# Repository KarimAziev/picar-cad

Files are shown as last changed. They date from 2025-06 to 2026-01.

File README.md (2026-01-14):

# About

This repository contains the 3D model source files for a four-wheeled robot chassis and steering system, written entirely in [OpenSCAD](https://openscad.org/). The design supports 3D printing and does not rely on external libraries.

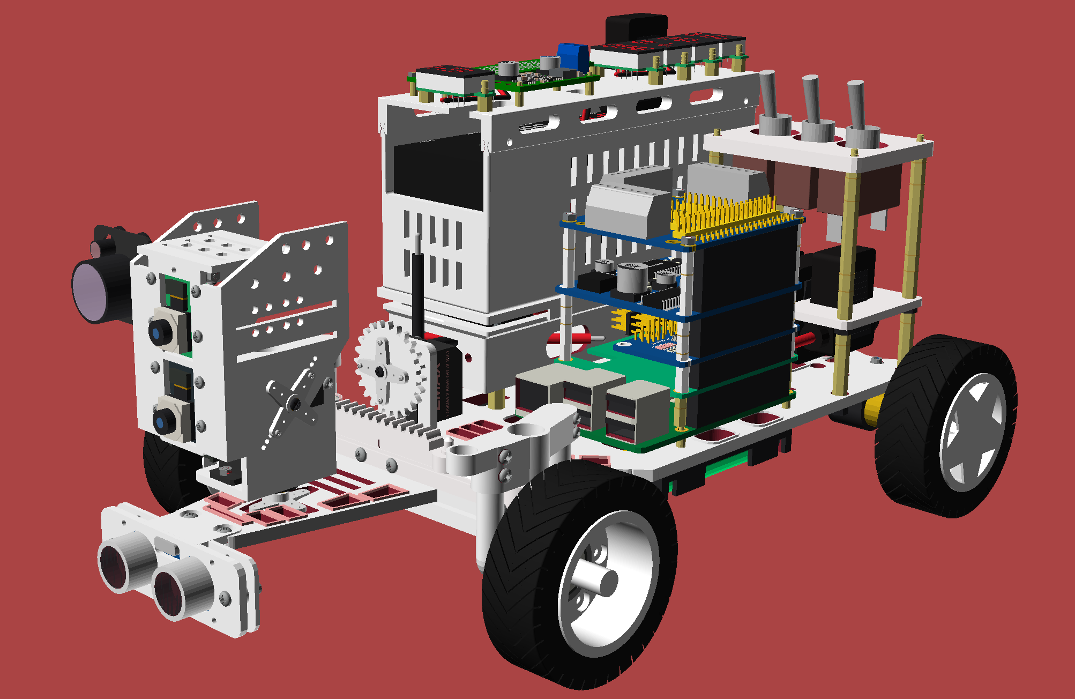
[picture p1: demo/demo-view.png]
Main View

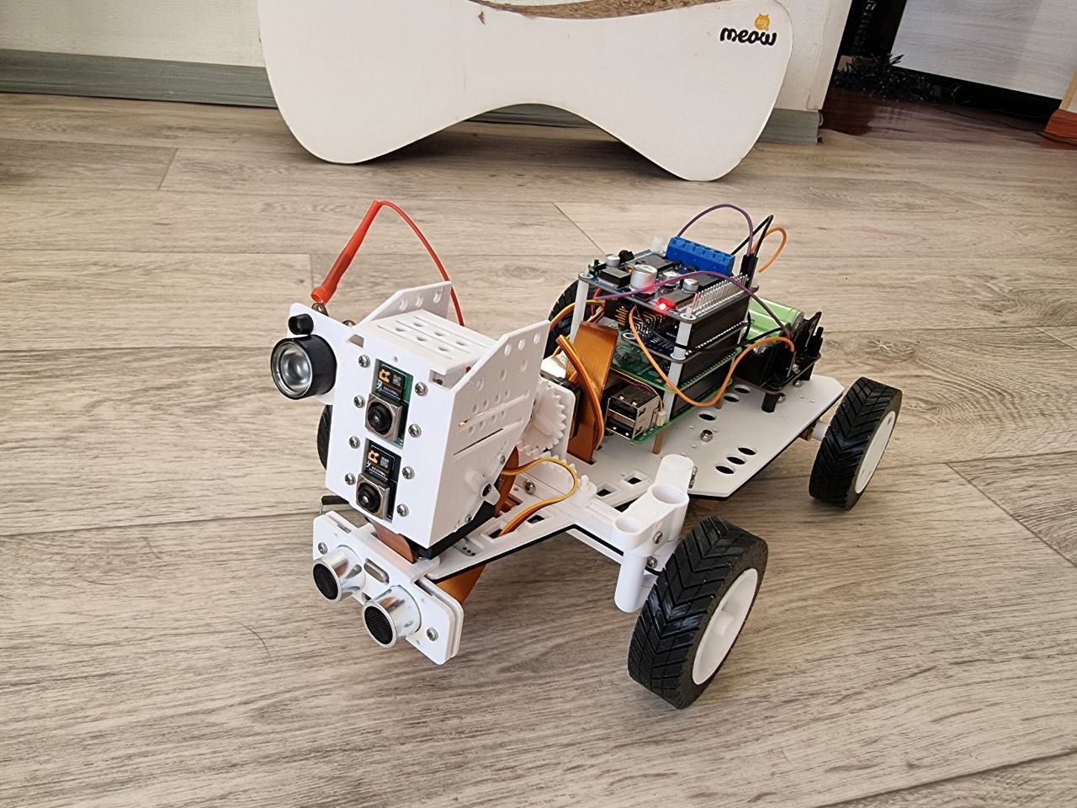
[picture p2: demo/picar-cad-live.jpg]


<!-- markdown-toc start - Don't edit this section. Run M-x markdown-toc-refresh-toc -->

**Table of Contents**

> - [About](#about)
>   - [Overview](#overview)
>     - [Requirements](#requirements)
>     - [CLI workflows (Makefile)](#cli-workflows-makefile)
>     - [Configurations](#configurations)
>     - [Validation (quick commands)](#validation-quick-commands)
>   - [Ackermann Geometry](#ackermann-geometry)
>   - [Assembly](#assembly)
>   - [Structure](#structure)
>   - [External Details](#external-details)
>     - [Bearings](#bearings)
>     - [Servos](#servos)
>     - [Raspberry Pi](#raspberry-pi)
>     - [Power Supply](#power-supply)
>       - [A Turnigy Rapid-style hardcase LiPo](#a-turnigy-rapid-style-hardcase-lipo)
>       - [UPS module S3](#ups-module-s3)
>       - [Preset swap checklist](#preset-swap-checklist)
>       - [Battery holders](#battery-holders)
>     - [Motors](#motors)
>     - [Camera Module](#camera-module)
>     - [Ultrasonic](#ultrasonic)
>     - [Switch buttons and fuses](#switch-buttons-and-fuses)
>     - [IR LED](#ir-led)
>     - [Bolts, Nuts and Standoffs](#bolts-nuts-and-standoffs)
>       - [Steering panel](#steering-panel)
>       - [Steering pinion](#steering-pinion)
>         - [For Servo gear](#for-servo-gear)
>         - [Self-tapping bolts for servo arm](#self-tapping-bolts-for-servo-arm)
>       - [Steering Knuckle](#steering-knuckle)
>       - [Raspberry Pi](#raspberry-pi-1)
>       - [Power case stack (default LiPo setup)](#power-case-stack-default-lipo-setup)
>         - [Shared bolts](#shared-bolts)
>         - [Socket case and lid](#socket-case-and-lid)
>         - [Power case and lid](#power-case-and-lid)
>       - [Battery holder](#battery-holder)
>       - [UPS module S3](#ups-module-s3-1)
>       - [Motor brackets](#motor-brackets)
>         - [For two N20 motors](#for-two-n20-motors)
>         - [For two standard (yellow) motors](#for-two-standard-yellow-motors)
>       - [Head](#head)
>         - [For two Raspberry Pi Camera Module 3 boards](#for-two-raspberry-pi-camera-module-3-boards)
>       - [Head neck](#head-neck)
>       - [IR Case for the Infrared LED Light Board](#ir-case-for-the-infrared-led-light-board)
>       - [Ultrasonic case for HC-SR04](#ultrasonic-case-for-hc-sr04)
>       - [Wheel hubs](#wheel-hubs)
>     - [Switch buttons and fuses](#switch-buttons-and-fuses-1)
>   - [Full BOM (default preset)](#full-bom-default-preset)
>   - [Full BOM (with UPS module S3)](#full-bom-with-ups-module-s3)

<!-- markdown-toc end -->

## Overview

The robot model is designed around the following core elements:

- **Ackermann Steering**: This design implements Ackermann steering and computes the steering radii from the robot parameters (not just by making the inner wheel turn more). The model calculates the trapezoid geometry automatically so you usually don’t need to tweak Ackermann-specific variables by hand.
- **Rear-Wheel Drive**: Two individual motors drive the rear wheels. Both standard yellow DC motors and N20-type motors are supported.
- **Modular Head Mount**: The head mount is designed to accommodate two Raspberry Pi Camera Module 3 or more sensors (e.g., day/night configuration).
- **Extendable Power Tiers**: Default power case for high-discharge LiPo packs (e.g., Turnigy Rapid 4S2P) plus battery holders plus slots for servo/motor driver HATs; Waveshare UPS S3 remains optional.
- **Raspberry Pi**: The chassis includes placements and bolt holes for the Raspberry Pi 5 and multiple 18650 battery holders.

### Requirements

Since `textmetrics` is used throughout the project, a nightly build of OpenSCAD is required. Also, be sure to enable `textmetrics` in the OpenSCAD editor via `Preferences -> Features -> textmetrics`. When using the CLI, pass `--enable=textmetrics` (e.g., `openscad --enable=textmetrics --backend=Manifold ...`).

### CLI workflows (Makefile)

- `make help` — list available targets.
- `make tests` — run all `tests/test_*.scad` suites; tolerates the empty top-level warning used by logic-only tests.
- `make assembly` — export `scad/assembly.scad` to `build/export/stl/assembly.stl` and `build/export/3mf/assembly.3mf` with `--backend=Manifold --enable=textmetrics --hardwarnings` and 3MF metadata.
- `make printable` — export `scad/printable.scad` and every file in `scad/printable_parts/` to flattened `build/export/stl/` and `build/export/3mf/` (tires prefer the TPU material hint; falls back if unsupported).
- `make all` — run tests, then build assembly and all printable exports.
- `make clean` — remove build outputs and test temp files.

### Configurations

Two main presets are supported: the default LiPo power case stack and the UPS S3 option. Both assume two battery holders. Jump to the BOMs for details: [Full BOM (default preset)](#full-bom-default-preset) or [Full BOM (with UPS module S3)](#full-bom-with-ups-module-s3).

### Validation (quick commands)

All commands require `--enable=textmetrics --backend=Manifold`.

```sh
# Full assembly preview (PNG)
openscad -o /tmp/scad-preview.png --preview --imgsize=754,934 --backend=Manifold --enable=textmetrics --camera=0,0,0,0,0,0,1100 scad/assembly.scad

# Utility tests
openscad --backend=Manifold --enable=textmetrics -o /tmp/test_functions.stl tests/test_functions.scad
openscad --backend=Manifold --enable=textmetrics -o /tmp/test_plist.stl tests/test_plist.scad
```

## Ackermann Geometry

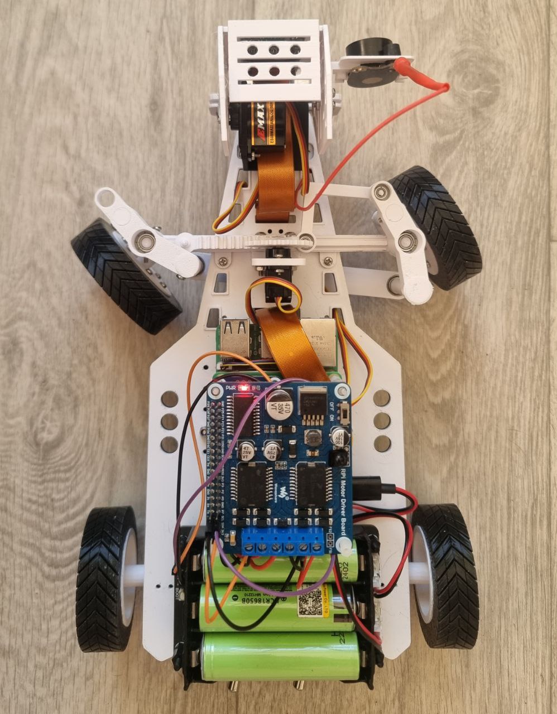
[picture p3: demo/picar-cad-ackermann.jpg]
Ackermann steering view


Ackermann steering is implemented with a rack-and-pinion mechanism that drives a single L-link (`rack_link`) mounted to one knuckle. That knuckle rotates when the rack moves, the opposite knuckle follows through a tie rod. The knuckles and tie rod form the Ackermann trapezoid, so the inside wheel turns more than the outside wheel.

> [!NOTE]
> Install the `rack_link` on only one side and on only one of the knuckles - it doesn't matter which. Movement of the rack will cause that "leading" knuckle to rotate. The leading knuckle is then connected to the second, "driven" knuckle via a tie rod.

Most parameters live in `scad/parameters.scad`, but the actual Ackermann geometry (angles and the required tie-rod top width) is calculated automatically from core robot dimensions such as chassis length, steering panel placement and knuckle geometry. Because of that, you will rarely need to edit Ackermann-specific variables manually - especially `steering_angle_deg`, which is derived from the layout.

## Assembly

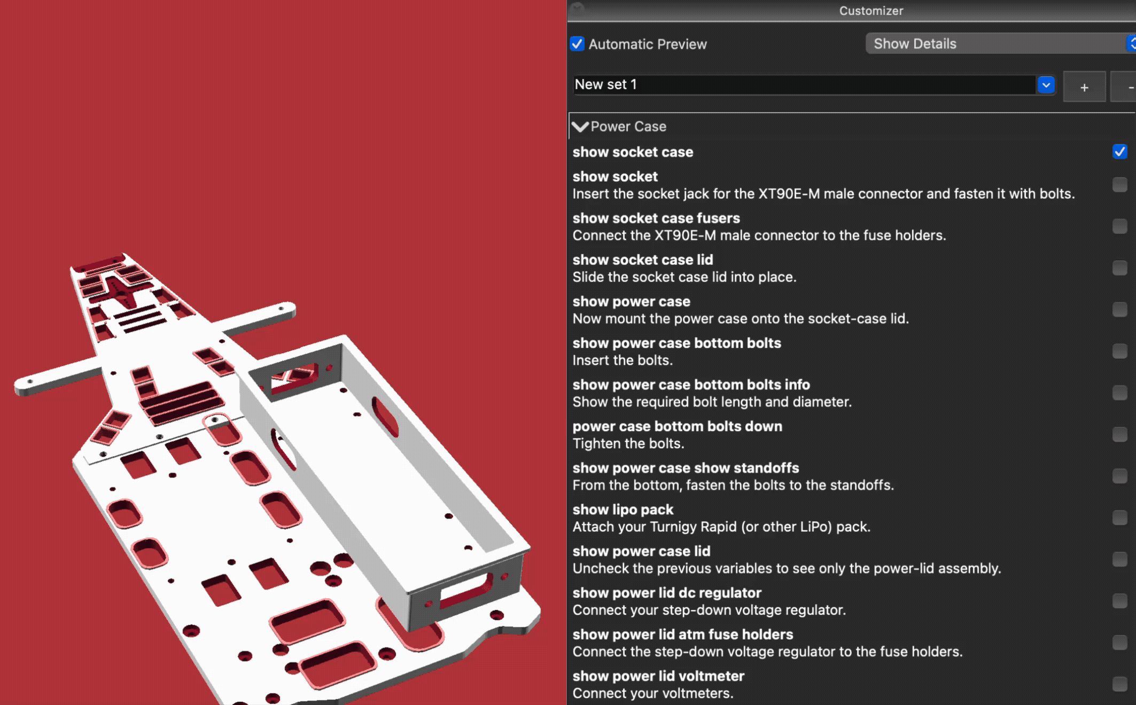
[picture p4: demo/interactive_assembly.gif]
Interactive Assembly


The interactive guide lives in `scad/assembly_guide.scad`. Open it in OpenSCAD and step through the boolean checkboxes in the built-in Customizer to reveal each assembly step (power case, steering, electronics, and wheels). For a static full build view, use `scad/assembly.scad`.

## Structure

The project is organized into several reusable modules under the scad/ directory:

- `parameters.scad`: Central configuration file containing physical dimensions (units are in millimeters).
- `power_lid_parameters.scad`: Configuration for the power case lid.
- `printable.scad`: Contains all printable parts in one place. You can print all parts except the tires using either PETG (recommended) or PLA. For the tires, use TPU (e.g., TPU 95A).
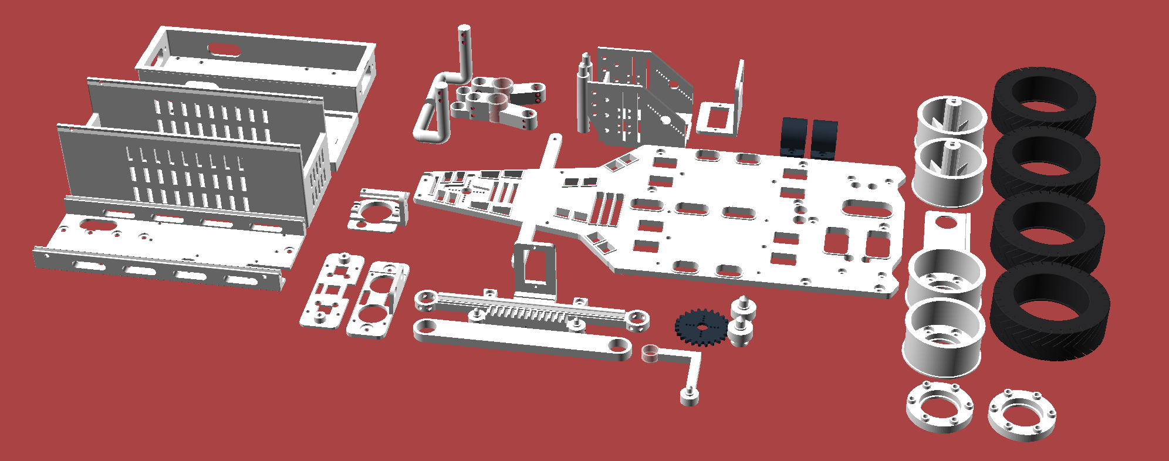
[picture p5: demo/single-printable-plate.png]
Single printable view
  
- `printable_parts/`: Individual printable part sources (one part per file) used by the Makefile for per-part exports.
- `assembly.scad`: Fully assembled view of the robot.
  Overview
- `assembly_guide.scad`: Interactive assembly. See [above](#assembly).
- `steering_system/`: Rack-and-pinion steering system based on Ackermann geometry.
- `power/`: Power case and related components.
- `components/chassis/`: Chassis and other components.
- `head/`: Mounting system for dual Raspberry Pi cameras.
- `motor_brackets/`: Brackets for both standard (yellow) and N20-style motors.
- `wheels/`: Components for rear and front wheels, including hubs and tires.
- `placeholders/`: Placeholder geometry for components such as the Raspberry Pi, servos, DC motors, battery holders, HATs, sensors, step-down voltage converters, INA260, etc. There’s a lot of stuff in there.
- `lib/`: Reusable modules. One important module is `lib/plist`, which provides helpers for working with property lists-a dict-like data structure used throughout the project because OpenSCAD doesn’t support dictionaries.

## External Details

All these details are just recommendations, you can use any other details, just don't forget to specify corresponding dimensions in `parameters.scad` and `power_lid_parameters.scad`. Reference renders and photos live in `demo/` (e.g., `demo/top-view.png`, `demo/ups_module_s3.png`, `demo/head_neck.png`, `demo/ultrasonic.png`).

### Bearings

- Four 685 (5x11x5) bearings: two are inserted into the steering knuckles and mounted on kingpin posts. To use different sizes, modify the variables `knuckle_bearing_outer_dia`, `knuckle_bearing_inner_dia`, and other relevant variables. The other two are inserted into the tie rod; the corresponding variables are `tie_rod_bearing_outer_dia`, `tie_rod_bearing_inner_dia`, and others.
- Two 693 (3x8x4) bearings are inserted into the rack link and into the knuckle arm that connects to the rack link. Both flanged and standard versions are supported.
- Two 608 (8x22x7) bearings are inserted into the front wheels.

### Servos

This project supports three **EMAX ES08MA II** servos by default. If using different models, update the following variables in `parameters.scad`:

- `steering_servo_slot_width` and `steering_servo_slot_height` for the steering servo
- `head_neck_pan_servo_slot_width` and `head_neck_pan_servo_slot_height` for the pan servo
- `head_neck_tilt_servo_slot_width` and `head_neck_tilt_servo_slot_height` for the tilt servo

### Raspberry Pi

Raspberry Pi 5 is supported by default. To use a different model, adjust the relevant variables prefixed with `rpi_` (e.g., `rpi_bolt_spacing`).

### Power Supply

#### A Turnigy Rapid-style hardcase LiPo

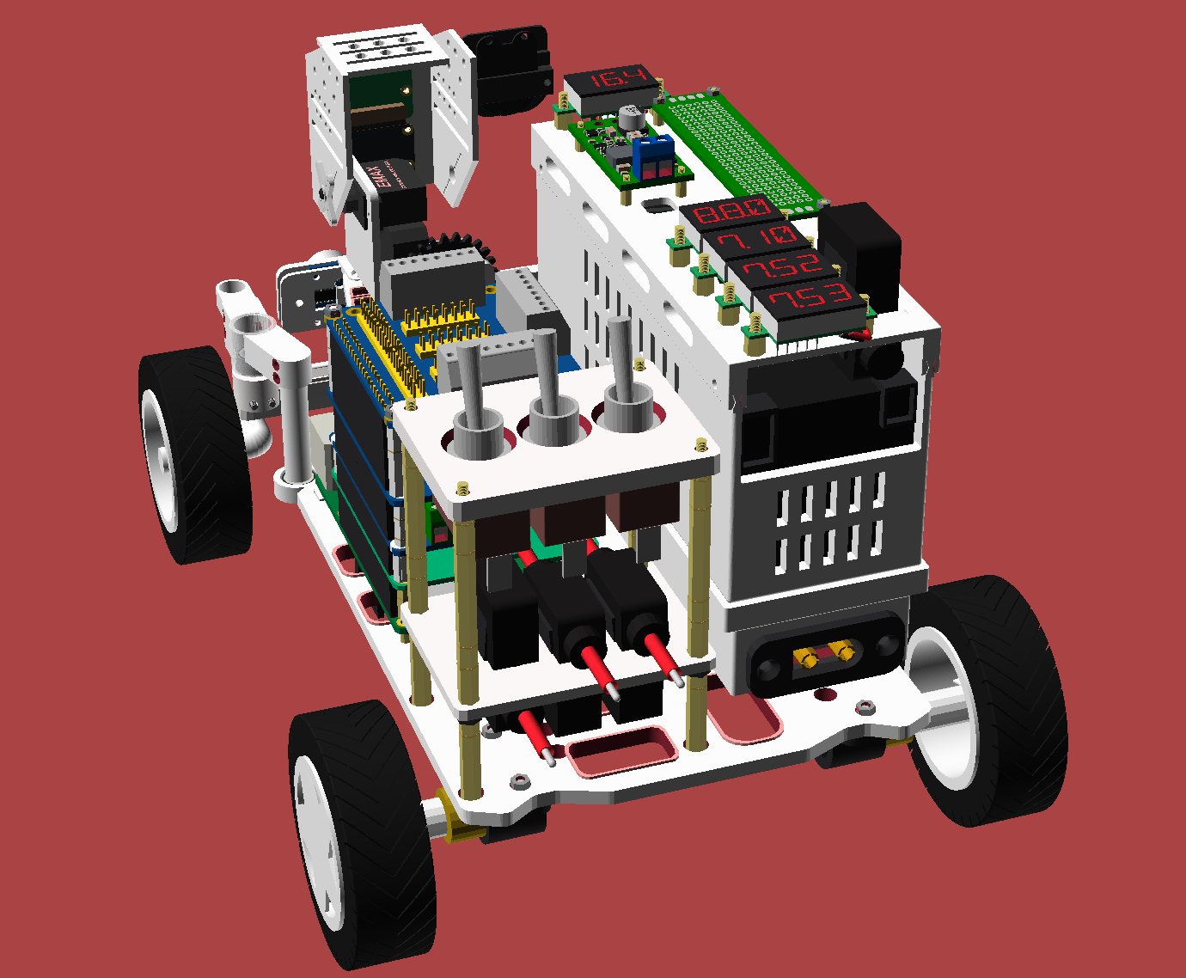
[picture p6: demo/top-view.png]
Power case


The default power source is a modular power case sized for a Turnigy Rapid-style hardcase LiPo (see the `lipo_pack_*` and `power_case_*` parameters). The lid supports an XT90E connector, blade fuses, a voltmeter, and a step-down regulator. Rails/clamps keep the pack fixed.

#### UPS module S3

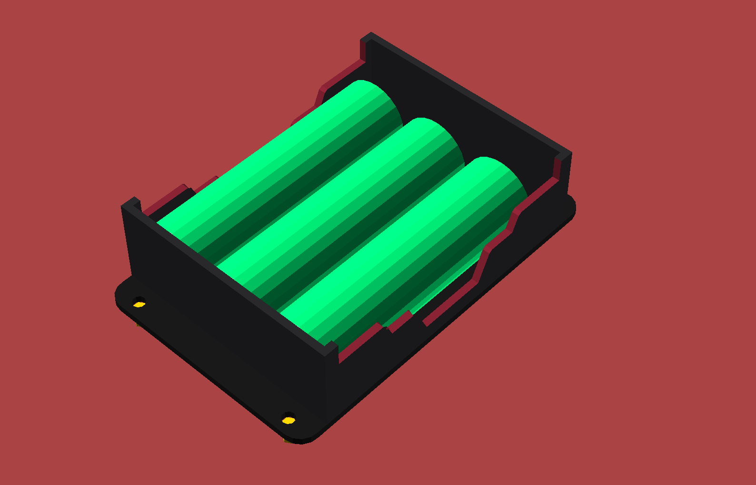
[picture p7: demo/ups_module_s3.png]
UPS module S3


The Waveshare [UPS module S3](https://www.waveshare.com/wiki/UPS_Module_3S) is still supported, but it is no longer the default because it is not reliable enough.

If you want to use it, enable it in `parameters.scad`:

```scad
battery_ups_holes_enabled = true;
```

And in `assembly.scad`:

```scad
show_ups_hat = true;
```

You will likely also need to adjust the layout parameters for the Raspberry Pi (`rpi_chassis_y_position` and `rpi_chassis_x_position`) and perhaps disable the power case module (see the `power_*` variables).

#### Preset swap checklist

- Toggle UPS on/off: set `battery_ups_holes_enabled` in `parameters.scad` and `show_ups_hat` in `assembly.scad`.
- Enable/disable the power case stack via the `power_*` variables when switching to UPS.
- Reposition the Raspberry Pi for UPS clearance using `rpi_chassis_y_position` and `rpi_chassis_x_position`.
- Keep two battery holders enabled by default (adjust `chassis_body_battery_holders_specs` if you change count/placement).

#### Battery holders

Battery holders with different settings are supported; the presets assume two holders by default. Variables prefixed with `battery_holder*` control the default values, so you can combine different holders and settings by editing `chassis_body_battery_holders_specs`, a property list that takes precedence over the global variables.

**By mount type**

`battery_holder_mount_type` holds the global mount type: either `under_cell` (holes under each cell intercell) or `intercell` (holes between the cells). The default is `intercell`.

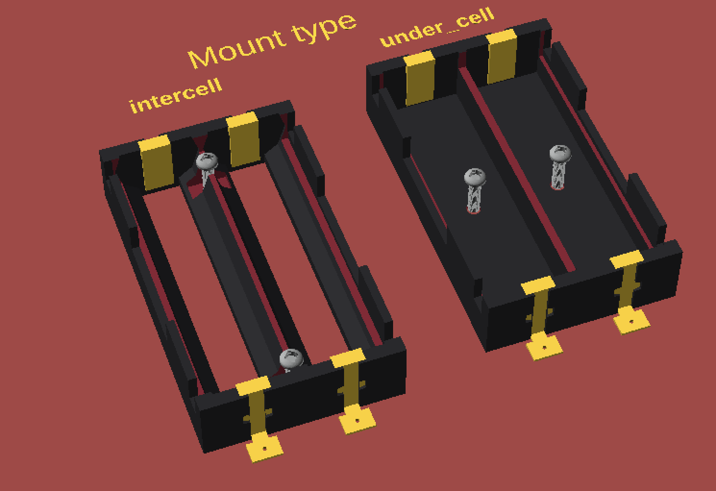
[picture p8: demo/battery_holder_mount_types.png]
Mount Types


**By terminal type**

`battery_holder_terminal_type` holds the global terminal type: `solder_tab` (rectangular external tabs) or `coil_spring` (circular contact with a helical spring, positive polarity). `solder_tab` (default) will also create additional slots for the contacts in the chassis.

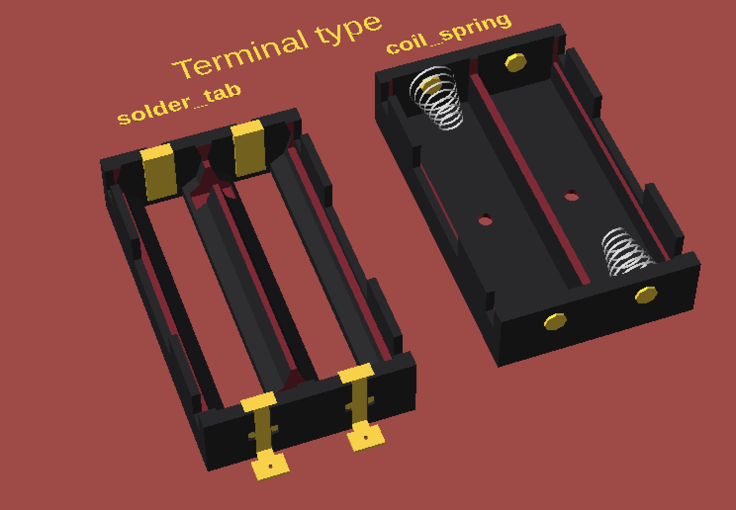
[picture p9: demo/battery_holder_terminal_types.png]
Terminal Types


You can create as many battery holders and slots for them as you want. Here is a quick example:

```scad
chassis_body_battery_holders_specs =
  ["type", "grid",
   "size", [chassis_body_w, chassis_body_len],
   "rows",
   maybe_add_battery_holders_rows_h(
      [["cells",
        [["w", 0.5,
          "placeholder",
          ["placeholder_type", "battery_holder",
           "mount_type", battery_holder_mount_type,
           "count", 3,
           "show_battery", true,
           "terminal_type", battery_holder_terminal_type,
           "side_wall_cutout_type", battery_holder_side_wall_type]],
         ["w", 0.5,
          "placeholder",
          ["placeholder_type", "battery_holder",
           "terminal_type", "coil_spring",
           "side_wall_cutout_type", "enclosed",
           "battery_len", 70,
           "battery_dia", 21,
           "show_battery", true,
           "mount_type", "under_cell",
           "battery_color", "pink",
           "color", "black"]]]],
       ["cells",
        [["w", 0.5,
          "spin", 90,
          "placeholder",
          ["placeholder_type", "battery_holder",
           "show_battery", true,
           "count", 1,
           "mount_type", battery_holder_mount_type,
           "terminal_type", battery_holder_terminal_type,
           "side_wall_cutout_type", battery_holder_side_wall_type]]]]])];
```

Result:

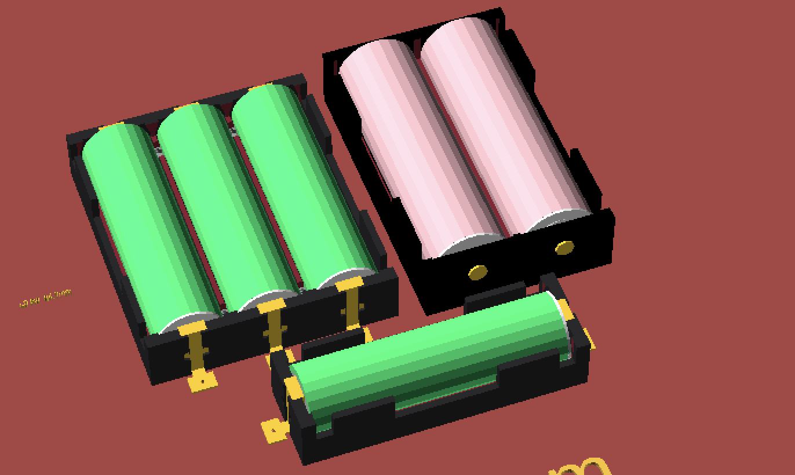
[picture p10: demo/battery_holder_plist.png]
Custom battery holders


### Motors

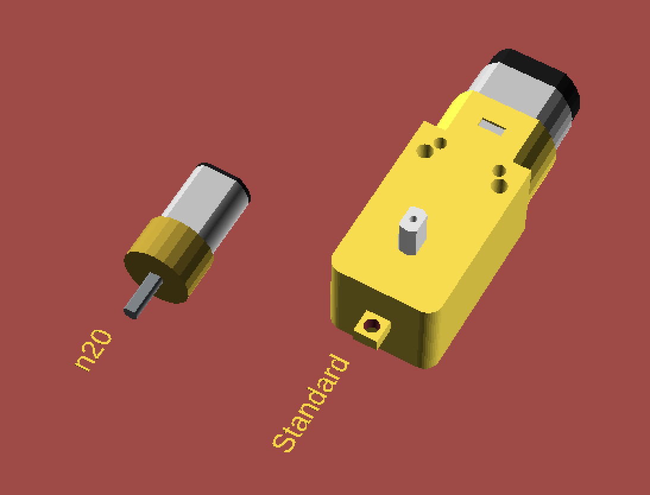
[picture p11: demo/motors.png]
Motors


Two rear motors are supported-either standard or N20-type:

- The "n20" type refers to motors like the **GA12-N20** with a 3 mm shaft.
- The "standard" type refers to widely available yellow gear motors with a 5 mm shaft.

Rear wheel shaft size depends on the motor type. Use the variable `motor_type` in `parameters.scad` to set the proper shaft diameter.

### Camera Module

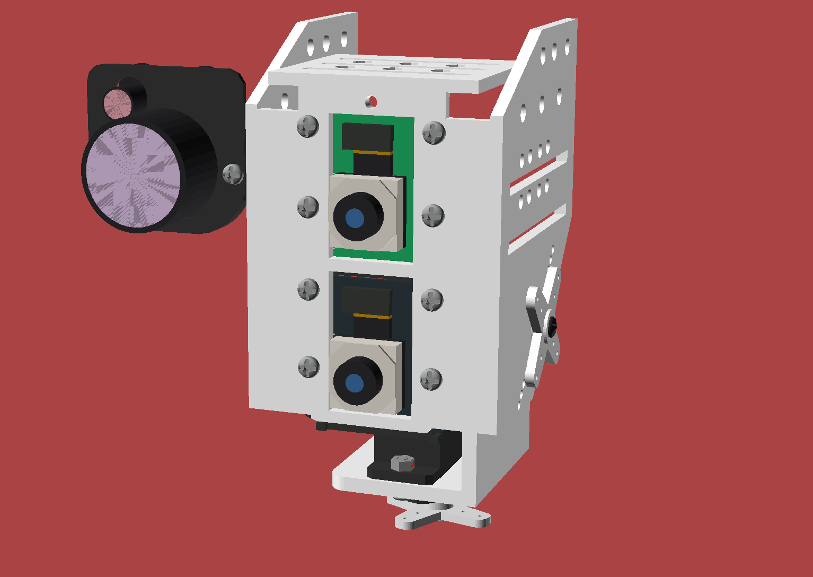
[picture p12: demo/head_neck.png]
Camera


The design supports one, two or more camera modules. The default dimensions are compatible with the Raspberry Pi Camera Module 3.

### Ultrasonic

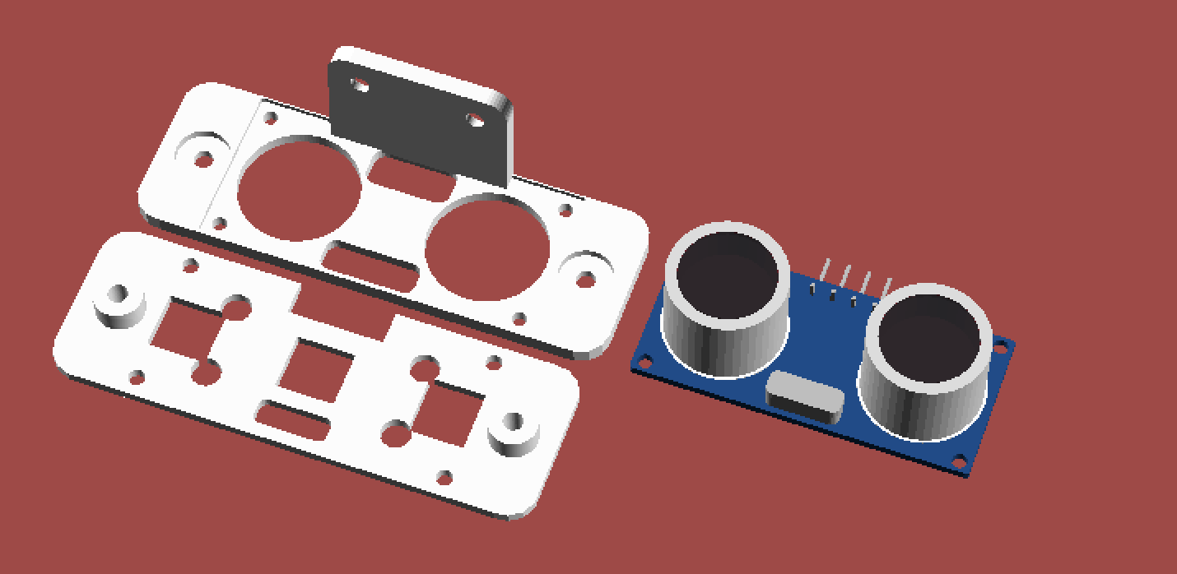
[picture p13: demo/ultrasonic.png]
Ultrasonic


The model supports the HC-SR04 ultrasonic sensor.

### Switch buttons and fuses

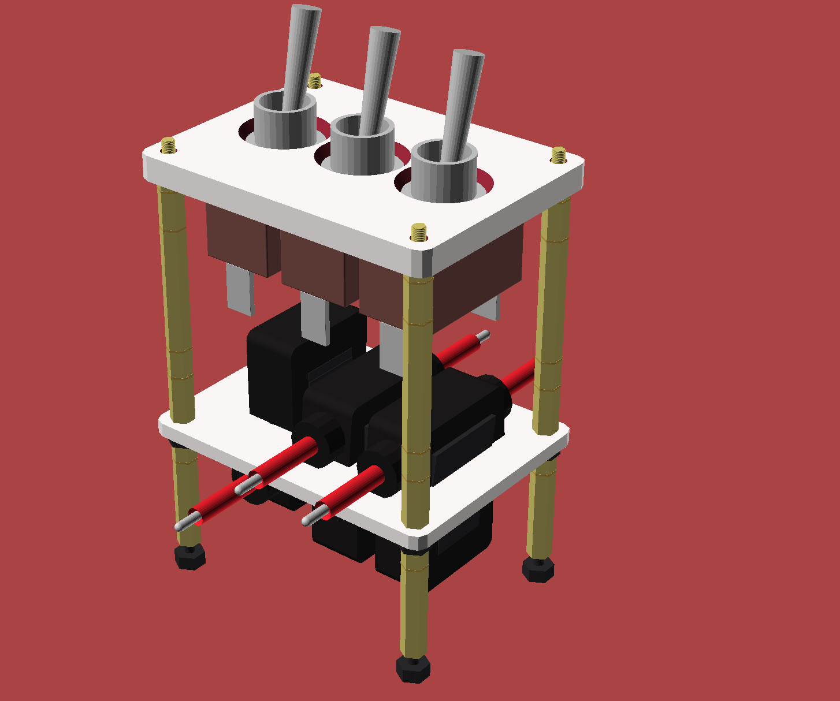
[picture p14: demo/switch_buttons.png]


Switch buttons with a circular mounting type are supported, as well as two types of fuse holders: ATM and ATC mini.

### IR LED

The design also supports case for [IR Waveshare Infrared LED Light Board Module](https://www.waveshare.com/infrared-led-board.html).

The original LED board is incompatible with the Raspberry Camera Module 3, and the quality of Waveshare’s original camera is unsatisfactory.

Nevertheless, this LED board can be used with Camera Module 3 and other Raspberry Pi cameras. To do so, solder two wires (**GND** and **V+**) to the bolt holes on the LED board (the bolt holes serve both for mechanical attachment and for power). Then connect the positive wire to **3.3V** and the ground wire to **GND**.

### Bolts, Nuts and Standoffs

Since the default chassis thickness is **4 mm** (changeable via the variable `chassis_thickness`), use bolts at least **8 mm** long for fastenings that go through the chassis, depending on the nuts. I suggest using lock nuts for these bolts, but plain nuts are also acceptable.

The tables below are grouped by component. Pick only the sections relevant to your build.

Each table includes a "Variable" column that refers to a configurable variable in parameters.scad. You can change it to the bolt diameter you want to use.

#### Steering panel

| Size | Length (mm) | Amount | Nuts | Variable |
| --- | --- | --- | ---- | --- |
| M2.5 | 8 | 4 | 2 | `steering_panel_hinge_bolt_dia` |
| M2 | 8 | 2 | 2 | `steering_servo_bolt_dia` |
| M3 | 20 | 2 | 2 | `steering_servo_mount_connector_bolt_dia` |
| M2 or M2.5 for tight fit | 10 | 4 | 4 | `steering_kingpin_post_bolt_dia` |

#### Steering pinion

Your servo pack should already include bolts, a servo arm, and self-tapping bolts to secure the servo arm, but I'll list them here for reference as well.

##### For Servo gear

| Size | Length (mm) | Amount | Nuts | Variable |
| ---- | --- | --- | ---- | --- |
| M2 | 4 | 1 | 0 | `steering_servo_bolt_dia` |

> [!TIP]
> The variable `steering_servo_bolt_dia` is used only in assembly views, but there are useful variables that define the diameter of the hole at the center of the pinion where you insert the servo's gearbox - `steering_pinion_center_hole_dia`. Its default size is **6.5** mm.

##### Self-tapping bolts for servo arm

Self-tapping bolts should also be included in your pack. The diameter may differ slightly, but the bolts should still fit due to the nature of self-tapping bolts.

| Size | Length (mm) | Amount | Nuts | Variable |
| ---- | --- | --- | ---- | --- |
| M1.5 | 4 | 2 or more | 0 | `steering_pinion_screw_dia` |

#### Steering Knuckle

| Size | Length (mm) | Amount | Nuts | Variable |
| --- | --- | --- | ---- | --- |
| M2.5 | 10 | 4 (2 per knuckle) | 0 | `knuckle_shaft_bolt_dia` |
| M2 or M2.5 for tight fit | 10 | 4 (2 per knuckle) | 0 | `tie_rod_shaft_bolt_dia` |

#### Raspberry Pi

The exact bolt length depends on the standoffs you use. Since the default chassis thickness is 4 mm, you should use bolts that are at least 6 mm long.

| Size | Length (mm) | Amount | Nuts/Standoffs | Variable |
| ---- | --- | --- | --- | --- |
| M2 | 6 or higher | 4 | 4 (both nuts and standoffs) | `rpi_bolt_hole_dia` |

#### Power case stack (default LiPo setup)

Power case stack consists of four components:

- The socket case at the bottom, which holds the XT90E-M male connector and the fuse holder. It has four mounting holes for M3 standoffs that will secure it to the chassis.
- The socket’s sliding lid, also with four holes of the same spacing and size.
- The power case for a LiPo pack (e.g., Turnigy Rapid). It also has four holes of the same spacing and size as the socket components. It is mounted above the socket’s sliding lid and secured with four long M3 bolts that thread into the socket’s standoffs.
- The power case lid, with slots for a DC voltage regulator, voltmeters, a fuse holder, etc. Four M2.5 bolts clamp the lid rails, keep them short to avoid piercing the thin side walls.

##### Shared bolts

| Size | Length (mm)  | Amount | Standoffs | Variable |
| ---- | --- | --- | --- | --- |
| M3 | 31 or higher | 4 | 4 | `power_case_bottom_bolt_dia` |

##### Socket case and lid

| Size | Length (mm)  | Amount | Nuts | Variable |
| ---- | --- | --- | ---- | --- |
| M3 | 12 or higher | 2 | 2 | `xt90e_mount_dia` or `power_socket_case_jack_plist` [^1] |

[^1]: `xt90e_mount_dia` is a default value used in `power_socket_case_jack_plist`, which is a property list (a dict-like data structure) used throughout the project because OpenSCAD doesn’t support dictionaries. Unlike JSON, it uses a comma (`,`) instead of a colon (`:`). To change the diameter of the mounting holes for the XT90E-M connector only for the socket case, edit the `mount_dia` property in `power_socket_case_jack_plist`.

##### Power case and lid

**Bolts:**

| Size | Length (mm) | Amount | Nuts | Variable |
| ---- | --- | --- | ---- | --- |
| M2.5 | 6 | 4 | 4 | `power_case_rail_bolt_dia` |

**Step-down voltage regulator slot on the lid:**

By default, the slot fits the Pololu D24VXF5 step-down voltage regulator.

| Size | Length (mm) | Amount | Standoffs | Variable |
| ---- | --- | --- | --- | --- |
| M2 | 4 or higher | 4 | 4 | `step_down_voltage_bolt_hole_dia` |

**Voltmeters:**

By default, there are five slots for voltmeters, with two holes for each. To change the number of bolts to four, edit `power_lid_left_slots` in `scad/power_lid_parameters.scad`. Find the entry with the `"placeholder"` property set to `"voltmeter"`. Change `slot_size` to the desired spacing.

The default `slot_size` is `[0, 27.70]` (the X and Y spacing for the four corner mounting bolt positions). If you change it, for example, to `[10, 27.70]`, four holes will be created.

| Size | Length (mm) | Amount | Standoffs | Variable |
| ---- | --- | --- | --- | --- |
| M3 | 4 or higher | 2 | 2 (per slot) | `voltmeter_bolt_dia` |

#### Battery holder

| Size | Length (mm) | Amount | Nuts | Variable |
| ---- | --- | --- | ---- | --- |
| M3 | 8 or higher | 2 (per one) | 2 | `battery_holder_bolt_dia` |

#### UPS module S3

You should use either 4 or 8 M3 standoffs. If you use 8 standoffs, the nuts listed below are not needed.

| Size | Length (mm) | Amount | Nuts | Variable |
| ---- | --- | --- | ---- | --- |
| M3 | 8 or higher | 4 | 4 | `battery_ups_bolt_dia` |

#### Motor brackets

##### For two N20 motors

| Size | Length (mm) | Amount | Nuts | Variable |
| ---- | --- | --- | ---- | --- |
| M2.5 | 8 or higher | 4 | 4 | `n20_motor_bolt_dia` |

##### For two standard (yellow) motors

| Size | Length (mm) | Amount | Nuts | Variable |
| ---- | --- | --- | ---- | --- |
| M3 | 28 | 4 | 4 | `standard_motor_bracket_motor_bolt_hole` |
| M2 | 8 or higher | 4 | 4 | `standard_motor_bracket_chassis_bolt_hole` |

#### Head

##### For two Raspberry Pi Camera Module 3 boards

| Size | Length (mm) | Amount | Nuts | Variable |
| ---- | --- | --- | ---- | --- |
| M2 | 5 or higher | 8 (4 for each camera) | 8 | `head_camera_bolt_dia` |

As with the steering servo, your servo pack should already include bolts, a servo arm, and self-tapping bolts to secure the servo arm. The diameter of the hole on the head where the tilt-servo gearbox mounts is defined by `head_servo_mount_dia`.

The corresponding hole for the pan servo on the chassis is controlled by `chassis_pan_servo_slot_dia`.

#### Head neck

| Size | Length (mm) | Amount | Nuts | Variable |
| ---- | --- | --- | ---- | --- |
| M2 | 6 or higher | 2 | 2 | `head_neck_pan_servo_bolt_dia`  |
| M2 | 6 or higher | 2 | 2 | `head_neck_tilt_servo_bolt_dia` |

#### IR Case for the Infrared LED Light Board

| Size | Length (mm)  | Amount | Nuts | Variable |
| ---- | --- | --- | ---- | --- |
| M2 | 7 or higher  | 2 | 2 | `ir_case_bolt_dia` |
| M2 | 10 or higher | 2 | 2 | `ir_case_rail_bolt_dia` |

Variable `ir_case_bolt_dia` defines the diameter of the bolt holes that attach the case to the head; `ir_case_rail_bolt_dia` defines the diameter of the rail holes that secure the IR LED to the case itself.

#### Ultrasonic case for HC-SR04

| Size | Length (mm)  | Amount | Nuts | Variable |
| ---- | --- | --- | ---- | --- |
| M2.5 | 6 or higher  | 2 | 2 | `front_panel_connector_bolt_dia` |
| M2.5 | 10 or higher | 2 | 2 | `front_panel_bolt_dia` |

`front_panel_connector_bolt_dia` defines the diameter of the bolt hole on the bracket that connects to the chassis, and `front_panel_bolt_dia` defines the diameter of the bolt hole on the front panel that secures the ultrasonic sensor, which is placed between the front panel and the bracket.

#### Wheel hubs

Each wheel hub requires 6 M2.5 (or M3 for a very tight fit) bolts and nuts.

| Size | Length (mm)  | Amount | Nuts | Variable |
| --- | --- | --- | ---- | --- |
| M2.5 or M3 for tight fit | 12 or higher | 12 (6 per wheel hub) | 12 | `wheel_hub_bolt_dia` |

### Switch buttons and fuses

**Bolts**

| Size | Length (mm) | Amount | Nuts | Variable |
| ---- | --- | --- | ---- | --- |
| M3 | 6 or higher | 4 | 4 | `panel_stack_bolt_dia` |

**Standoffs**

Since the two panels are connected with standoffs, the required standoff height depends on the height of the fuse holders and switch buttons. Usually, you should use 6-8 standoffs (12-15 mm) for the button panel and four 12 mm standoffs for the fuse panel.

## Full BOM (default preset)

Assumes two battery holders are installed alongside the default LiPo power case stack. Currently using Waveshare 16-channel Servo Driver HAT and Waveshare RPi Motor Driver Board, but planning/recommending Pololu Dual MC33926 Motor Driver for Raspberry Pi and a Pololu servo driver HAT (model TBD).

**Core components**

- Printed parts from `scad/printable.scad` (PETG/PLA) and TPU tires
- 1x Raspberry Pi 5
- 3x EMAX ES08MA II servos (steering + pan + tilt)
- 2x N20 rear motors (default `motor_type`)
- 2x Raspberry Pi Camera Module 3
- 1x HC-SR04 ultrasonic sensor
- 1x IR Waveshare Infrared LED Light Board Module
- 1x Servo driver HAT, 1x motor driver HAT (see note above)
- 4x 685 bearings, 2x 693 bearings, 2x 608 bearings
- Turnigy Rapid-style 4S2P LiPo + XT90E connector, Pololu D24VXF5 regulator, 5x voltmeters, 4x fuse holders (between LiPo and toggle switch, toggle switch and RPi, one each for motor/servo HATs), 3x toggle switches
- 2x 18650 battery holders (see `battery_holder*` parameters)

**Hardware summary (see bolt lengths in the section above)**

Fuse routing: LiPo -> fuse -> toggle -> fuse -> RPi; dedicated fuses feed the motor and servo HATs.

| Subassembly | Bolts | Nuts | Standoffs/Notes |
| --- | --- | ---- | --- |
| Steering panel | M2.5×8 (4), M2×8 (2), M3×20 (2), M2/M2.5×10 (4) | 10 | — |
| Steering pinion | M2×4 (1), M1.5 self-tapping (2) | 0 | Uses servo arm hardware |
| Steering knuckles | M2.5×10 (4), M2/M2.5×10 (4) | 0 | — |
| Raspberry Pi | M2×6+ (4) | 4 | 4× standoffs |
| Power case stack (LiPo, socket, lid, regulator, voltmeters) | M3×31+ (4), M3×12+ (2), M2.5×6 (4), M2×4+ (4), M3×4+ for voltmeters (10) | 6 | 4× long M3 standoffs, 4× for regulator, 10× for voltmeters |
| Battery holders on chassis (2×) | M3×8+ (4) | 4 | — |
| Switch buttons & fuse panels | M3×6+ (4) | 4 | 6–8 standoffs (12–15 mm) for button panel, 4×12 mm for fuse panel |
| Motor brackets (N20 pair) | M2.5×8+ (4) | 4 | — |
| Head (2 cameras) | M2×5+ (8) | 8 | — |
| Head neck | M2×6+ (4) | 4 | — |
| IR case | M2×7+ (2), M2×10+ (2) | 4 | — |
| Ultrasonic bracket | M2.5×6+ (2), M2.5×10+ (2) | 4 | — |
| Wheel hubs (pair) | M2.5×12+ (12) | 12 | Use M3 for tighter fit |

## Full BOM (with UPS module S3)

Assumes two battery holders are installed; this variant omits the LiPo power case stack in favor of the UPS module S3. Currently using Waveshare 16-channel Servo Driver HAT and Waveshare RPi Motor Driver Board, but I am planning and recommending Pololu Dual MC33926 Motor Driver for Raspberry Pi and a Pololu servo driver HAT (model TBD).

**Core components**

- Printed parts from `scad/printable.scad` (PETG/PLA) and TPU tires
- 1x Raspberry Pi 5
- 3x EMAX ES08MA II servos (steering + pan + tilt)
- 2x N20 rear motors (default `motor_type`)
- 2x Raspberry Pi Camera Module 3
- 1x HC-SR04 ultrasonic sensor
- 1x IR Waveshare Infrared LED Light Board Module
- 1x Servo driver HAT, 1x motor driver HAT (see note above)
- 4x 685 bearings, 2x 693 bearings, 2x 608 bearings
- Waveshare UPS module S3 (+ 4 or 8 M3 standoffs), 3x toggle switches, 2x fuse holders (one each for motor/servo HATs), 5x voltmeters
- 2x 18650 battery holders (see `battery_holder*` parameters)

**Hardware summary (see bolt lengths in the section above)**

Fuse routing: UPS -> fuse -> RPi; dedicated fuses feed the motor and servo HATs.

| Subassembly | Bolts | Nuts | Standoffs/Notes |
| --- | --- | ---- | --- |
| Steering panel | M2.5×8 (4), M2×8 (2), M3×20 (2), M2/M2.5×10 (4) | 10 | — |
| Steering pinion | M2×4 (1), M1.5 self-tapping (2) | 0 | Uses servo arm hardware |
| Steering knuckles | M2.5×10 (4), M2/M2.5×10 (4) | 0 | — |
| Raspberry Pi | M2×6+ (4) | 4 | 4× standoffs |
| UPS module S3 mount | M3×8+ (4) | 4 | Use 4 or 8 M3 standoffs; nuts not needed with 8 standoffs |
| Battery holders on chassis (2×) | M3×8+ (4) | 4 | — |
| Switch buttons & fuse panels | M3×6+ (4) | 4 | 6–8 standoffs (12–15 mm) for button panel, 4×12 mm for fuse panel |
| Motor brackets (N20 pair) | M2.5×8+ (4) | 4 | — |
| Head (2 cameras) | M2×5+ (8) | 8 | — |
| Head neck | M2×6+ (4) | 4 | — |
| IR case | M2×7+ (2), M2×10+ (2) | 4 | — |
| Ultrasonic bracket | M2.5×6+ (2), M2.5×10+ (2) | 4 | — |
| Wheel hubs (pair) | M2.5×12+ (12) | 12 | Use M3 for tighter fit |

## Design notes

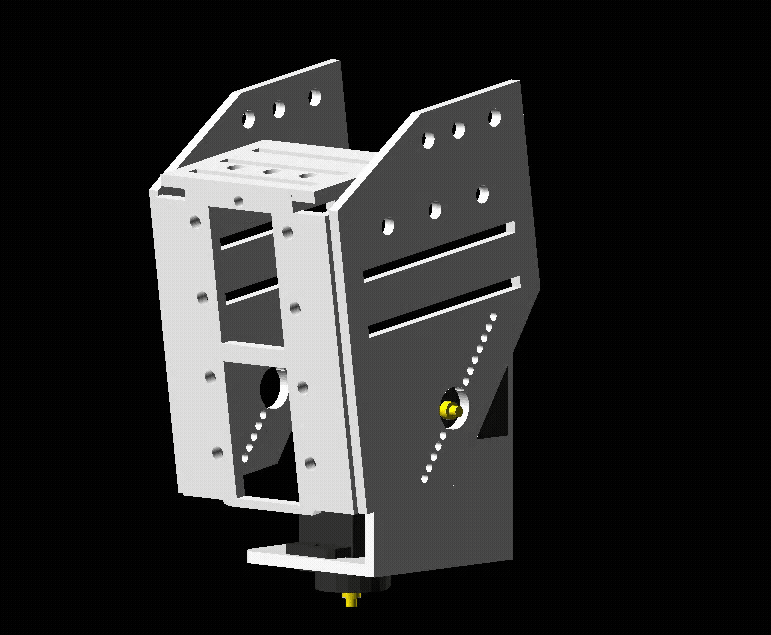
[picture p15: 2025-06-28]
demo/picar-cad-head-demo.gif

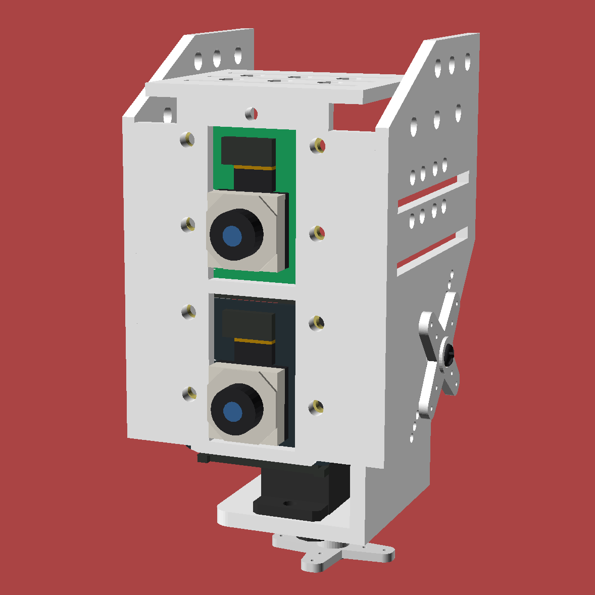
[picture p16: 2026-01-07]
demo/cameras.png

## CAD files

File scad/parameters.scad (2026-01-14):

/**
 * Module: Parameters
 * This file defines most of the robot parameters
 * All dimensions are in millimeters (mm)
 *
 * Author: Karim Aziiev <karim.aziiev@gmail.com>
 * License: GPL-3.0-or-later
 */

include <colors.scad>

use <lib/functions.scad>
use <lib/plist.scad>
use <placeholders/battery_holder/util.scad>
use <steering_system/knuckle_util.scad>

assembly_use_front_steering                          = false;
assembly_shaft_use_front_steering                    = true;

// ─────────────────────────────────────────────────────────────────────────────
// ATC ATO Blade Fuse Holder
// ─────────────────────────────────────────────────────────────────────────────

atc_ato_blade_fuse_holder_top_cover_h                = 35.3;
atc_ato_blade_fuse_holder_top_cover_w                = 27.10;
atc_ato_blade_fuse_holder_top_cover_thickness        = 13.9;
atc_ato_blade_fuse_holder_top_rad                    = 5;

atc_ato_blade_fuse_holder_top_joint_h                = 7.8;
atc_ato_blade_fuse_holder_top_joint_thickness        = 1.5;

atc_ato_blade_mounting_wall_h                        = 17.45;
atc_ato_blade_mounting_wall_w                        = 25.0;
atc_ato_blade_mounting_wall_thickness                = 3.30;

atc_ato_blade_fuse_holder_bottom_cover_h             = 12.22;
atc_ato_blade_fuse_holder_bottom_cover_w             = 24;
atc_ato_blade_fuse_holder_bottom_cover_thickness     = 14.56;
atc_ato_blade_fuse_holder_bottom_rad                 = 5;

// ─────────────────────────────────────────────────────────────────────────────
// Inline ATM fuse holder
// ─────────────────────────────────────────────────────────────────────────────

atm_fuse_holder_body_wiring_d                        = 3.8;
atm_fuse_holder_body_bottom_l                        = 28.50;
atm_fuse_holder_body_top_l                           = 28.9;
atm_fuse_holder_body_h                               = 15.070;
atm_fuse_holder_body_thickness                       = 12.20;

atm_fuse_holder_cap_thickness                        = 11.60;
atm_fuse_holder_cap_top_l                            = 24.60;
atm_fuse_holder_cap_bottom_l                         = 23.07;
atm_fuse_holder_cap_h                                = 21.64;

atm_fuse_holder_body_rib_thickness                   = 1.0;
atm_fuse_holder_body_rib_h                           = 10.00;
atm_fuse_holder_body_rib_l                           = 19.03;
// number of the ribs
atm_fuse_holder_body_rib_n                           = 5;

atm_fuse_holder_cap_rib_thickness                    = 1.0;
atm_fuse_holder_cap_rib_h                            = 14.30;

atm_fuse_holder_cap_rib_l                            = 13.3;
// number of the ribs
atm_fuse_holder_cap_rib_n                            = 7;
atm_fuse_holder_cap_rib_distance                     = 7.22;

atm_fuse_holder_mounting_hole_l                      = 22.0;
atm_fuse_holder_mounting_hole_h                      = 8.0;
atm_fuse_holder_mounting_hole_depth                  = 5.2;
atm_fuse_holder_mounting_hole_r                      = 5.0;

atm_fuse_holder_cap_hole_size                        = [atm_fuse_holder_mounting_hole_l * 0.8,
                                                        atm_fuse_holder_mounting_hole_h,
                                                        atm_fuse_holder_cap_h * 0.8];

// ─────────────────────────────────────────────────────────────────────────────
// Fuse holder
// ─────────────────────────────────────────────────────────────────────────────
fuse_panel_thickness                                 = 3;

atm_fuse_default_plist                               = ["placeholder", "atm_fuse_holder",
                                                        "type", "rect",
                                                        "slot_size", [atm_fuse_holder_mounting_hole_l + 1,
                                                                      atm_fuse_holder_mounting_hole_h + 2],
                                                        "corner_rad", atm_fuse_holder_mounting_hole_r,
                                                        "placeholder_size", [max(atm_fuse_holder_body_top_l,
                                                                                 atm_fuse_holder_body_bottom_l)
                                                                             + 12,
                                                                             atm_fuse_holder_body_thickness],
                                                        "body", ["size", [atm_fuse_holder_body_bottom_l,
                                                                          atm_fuse_holder_body_thickness,
                                                                          atm_fuse_holder_body_h,
                                                                          atm_fuse_holder_body_top_l],
                                                                 "corner_rad", 2,
                                                                 "round_side", "bottom",
                                                                 "rib", ["h", atm_fuse_holder_body_rib_h,
                                                                         "l", atm_fuse_holder_body_rib_l,
                                                                         "n", atm_fuse_holder_body_rib_n,
                                                                         "thickness", atm_fuse_holder_body_rib_thickness,
                                                                         "distance_from_top", 0]],
                                                        "wiring", ["d", atm_fuse_holder_body_wiring_d,
                                                                   "socket_type", "cylinder",
                                                                   "socket_type_len", 5,
                                                                   "color", red_1,
                                                                   "cut_len", 3,
                                                                   "left_pts", [[25, 0, 0]],
                                                                   "right_pts", [[25, 0, 0]]],
                                                        "color", matte_black_2,
                                                        "show_cap", true,
                                                        "show_body", true,
                                                        "cap_collar", ["size", [atm_fuse_holder_mounting_hole_l - 2,
                                                                                atm_fuse_holder_mounting_hole_h,
                                                                                atm_fuse_holder_mounting_hole_depth],
                                                                       "r", atm_fuse_holder_mounting_hole_r,
                                                                       "fuse_holes_spacing", [8, 4],
                                                                       "fuse_hole_size", [6.0, 1.82],
                                                                       "fuse_holes_pad_x", 4,
                                                                       "fuse_holes_pad_y", 0,
                                                                       "rib_thickness", 1,
                                                                       "rib_h", 0.8,
                                                                       "colr", matte_black,
                                                                       "rib_colr", matte_black_2,
                                                                       "rib_positions", [0.5]],
                                                        "cap", ["size", [atm_fuse_holder_cap_top_l,
                                                                         atm_fuse_holder_cap_thickness,
                                                                         atm_fuse_holder_cap_h,
                                                                         atm_fuse_holder_cap_bottom_l,],
                                                                "corner_rad", 2,
                                                                "round_side", "top",
                                                                "color", matte_black_2,
                                                                "rib", ["h", atm_fuse_holder_cap_rib_h,
                                                                        "l", atm_fuse_holder_cap_rib_l,
                                                                        "n", atm_fuse_holder_cap_rib_n,
                                                                        "thickness", atm_fuse_holder_cap_rib_thickness,
                                                                        "distance_from_top", atm_fuse_holder_cap_rib_distance]]];
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

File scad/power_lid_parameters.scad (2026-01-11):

include <colors.scad>
include <parameters.scad>

use <lib/functions.scad>
use <lib/plist.scad>

power_lid_left_slots  = [["type", "four_corner_holes",
                          "placeholder", "voltmeter",
                          "gap_before", -7,
                          "gap_after", 4,
                          "slot_size", [0, 27.70],
                          "bore_reverse", true,
                          "rotation", -90,
                          "x_offset", 0,
                          "y_offset", 0,
                          "d", voltmeter_bolt_dia,
                          "bore_d", voltmeter_bolt_dia * 2,
                          "bore_h", power_lid_thickness / 2,
                          "sink", false,
                          "display", ["size", [voltmeter_display_w,
                                               voltmeter_display_len,
                                               voltmeter_display_h],
                                      "upper_thickness", 1,
                                      "upper_color", matte_black,
                                      "bottom_color", "white"],
                          "hide_board", false,
                          "hide_display", false,
                          "text", "16.4",
                          "text_props", ["font", "DSEG14 Classic:style=Italic", "size", 6],
                          "pins", ["size", [voltmeter_pin_thickness,
                                            voltmeter_pin_h],
                                   "count", voltmeter_pins_count,
                                   "total_len", voltmeter_pins_len],
                          "wiring", ["d", voltmeter_wiring_d,
                                     "distance",
                                     voltmeter_wiring_distance,
                                     "path", [[-5, -5, -2],
                                              [-15, -10, -1],
                                              [10, -15, -2],
                                              [20, 0, 0]]],
                          "placeholder_size", [voltmeter_board_w,
                                               voltmeter_board_len,
                                               voltmeter_board_h]],
                         ["type", "custom",
                          "placeholder", "step_down_voltage_regulator",
                          "rotation", -90,
                          "d", step_down_voltage_bolt_hole_dia,
                          "placeholder_size", [step_down_voltage_regulator_len,
                                               step_down_voltage_regulator_w,
                                               step_down_voltage_regulator_thickness],
                          "terminal_size", step_down_voltage_screw_terminal_holes,
                          "slot_size", [step_down_voltage_regulator_len,
                                        step_down_voltage_regulator_w,
                                        step_down_voltage_regulator_thickness],
                          "bolt_spacing", [35.55, 15.2],
                          "vin_slot_offsets", [5, 0],
                          "vout_slot_offsets", [4, 0],
                          "vin_slot", [50.4, 9.5, 2.0],
                          "vout_slot", [8.4, 8.4, 2.0],
                          "gap_before", 2,
                          "gap_after", 27,
                          "align", -1,
                          "vin", ["thickness", step_down_voltage_screw_terminal_thickness,
                                  "isosceles_trapezoid", step_down_voltage_screw_terminal_isosceles_trapezoid,
                                  "base_h", step_down_voltage_screw_terminal_base_h,
                                  "top_l", step_down_voltage_screw_terminal_top_l,
                                  "top_h", step_down_voltage_screw_terminal_top_h,
                                  "contacts_n", step_down_voltage_screw_terminal_contacts_n,
                                  "contact_w", step_down_voltage_screw_terminal_contact_w,
                                  "contact_h", step_down_voltage_screw_terminal_contact_h,
                                  "pitch", step_down_voltage_screw_terminal_pitch,
                                  "bolt_spacing", [35.5, 5],
                                  "colr", step_down_voltage_screw_terminal_colr,
                                  "pin_thickness", step_down_voltage_screw_terminal_pin_thickness,
                                  "pin_h", step_down_voltage_screw_terminal_pin_h,
                                  "wall_thickness", step_down_voltage_screw_terminal_wall_thickness,],
                          "vout", ["thickness", step_down_voltage_screw_terminal_thickness,
                                   "isosceles_trapezoid", step_down_voltage_screw_terminal_isosceles_trapezoid,
                                   "base_h", step_down_voltage_screw_terminal_base_h,
                                   "top_l", step_down_voltage_screw_terminal_top_l,
                                   "top_h", step_down_voltage_screw_terminal_top_h,
                                   "contacts_n", step_down_voltage_screw_terminal_contacts_n,
                                   "contact_w", step_down_voltage_screw_terminal_contact_w,
                                   "contact_h", step_down_voltage_screw_terminal_contact_h,
                                   "pitch", step_down_voltage_screw_terminal_pitch,
                                   "bolt_spacing", [35.5, 5],
                                   "colr", step_down_voltage_screw_terminal_colr,
                                   "pin_thickness", step_down_voltage_screw_terminal_pin_thickness,
                                   "pin_h", step_down_voltage_screw_terminal_pin_h,
                                   "wall_thickness", step_down_voltage_screw_terminal_wall_thickness,]],
                         ["type", "four_corner_holes",
                          "placeholder", "voltmeter",
                          "gap_before", 0,
                          "gap_after", 2,
                          "slot_size", [0, 27.70],
                          "bore_reverse", true,
                          "rotation", -90,
                          "x_offset", 0,
                          "y_offset", 0,
                          "d", voltmeter_bolt_dia,
                          "bore_d", voltmeter_bolt_dia * 2,
                          "bore_h", power_lid_thickness / 2,
                          "sink", false,
                          "display", ["size", [voltmeter_display_w,
                                               voltmeter_display_len,
                                               voltmeter_display_h],
                                      "upper_thickness", 1,
                                      "upper_color", matte_black,
                                      "bottom_color", "white"],
                          "hide_board", false,
                          "hide_display", false,
                          "text", "8.8.0",
                          "text_props", ["font", "DSEG14 Classic:style=Italic", "size", 6],
                          "pins", ["size", [voltmeter_pin_thickness,
                                            voltmeter_pin_h],
                                   "count", voltmeter_pins_count,
                                   "total_len", voltmeter_pins_len],
                          "wiring", ["d", voltmeter_wiring_d,
                                     "distance",
                                     voltmeter_wiring_distance,
                                     "path", [[-5, -5, -2],
                                              [-15, -10, -1],
                                              [10, -15, -2],
                                              [20, 0, 0]]],
                          "placeholder_size", [voltmeter_board_w,
                                               voltmeter_board_len,
                                               voltmeter_board_h]],
                         ["type", "four_corner_holes",
                          "placeholder", "voltmeter",
                          "gap_before", 0,
                          "gap_after", 2,
                          "align", -1,
                          "slot_size", [0, 27.70],
                          "rotation", -90,
                          "bore_reverse", true,
                          "x_offset", 0,
                          "y_offset", 0,
                          "d", voltmeter_bolt_dia,
                          "bore_d", voltmeter_bolt_dia * 2,
                          "bore_h", power_lid_thickness / 2,
                          "sink", false,
                          "display", ["size", [voltmeter_display_w,
                                               voltmeter_display_len,
                                               voltmeter_display_h],
                                      "upper_thickness", 1,
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

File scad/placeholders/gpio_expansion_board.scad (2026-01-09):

/**
 * Module: GPIO Expansion Board
 *
 * Author: Karim Aziiev <karim.aziiev@gmail.com>
 * License: GPL-3.0-or-later
 */

include <../colors.scad>
include <../parameters.scad>

use <../lib/holes.scad>
use <../lib/placement.scad>
use <../lib/shapes2d.scad>
use <../lib/shapes3d.scad>
use <../lib/transforms.scad>
use <pad_hole.scad>
use <pin_header.scad>
use <screw_terminal.scad>
use <standoff.scad>

module gpio_expansion_board(show_standoff=true,
                            center=true,
                            show_nut=false,
                            extra_standoff_h=0) {
  w = gpio_expansion_size[0];
  l = gpio_expansion_size[1];
  h = gpio_expansion_size[2];

  translate([center ? 0 : w / 2, center ? 0 : l / 2, 0]) {
    union() {
      color(medium_blue_1, alpha=1) {
        linear_extrude(height=h, center=false) {
          difference() {
            rounded_rect(size=[gpio_expansion_size[0],
                               gpio_expansion_size[1]],

                         r=gpio_expansion_corner_rad,
                         center=true);
            four_corner_holes_2d(size=rpi_bolt_spacing, center=true);
            four_corner_holes_2d(size=gpio_expansion_bolt_spacing_2, center=true);
          }
        }
      }
      four_corner_children(size=rpi_bolt_spacing) {
        pad_hole(specs=gpio_expansion_mounting_hole_pad_spec,
                 thickness=h,
                 bolt_d=gpio_expansion_bolt_dia);
      }
      four_corner_children(size=gpio_expansion_bolt_spacing_2) {
        pad_hole(specs=gpio_expansion_mounting_hole_pad_spec,
                 thickness=h,
                 bolt_d=gpio_expansion_bolt_dia);
      }

      translate([-w / 2 + rpi_pin_header_width,
                 -l / 2
                 + rpi_pin_header_width
                 * rpi_pin_headers_cols / 2
                 + rpi_bolts_offset * 2,
                 -gpio_expansion_header_height]) {
        union() {
          pin_header(cols=rpi_pin_headers_cols,
                      rows=rpi_pin_headers_rows,
                      header_width=rpi_pin_header_width,
                      header_height=gpio_expansion_header_height,
                      pin_height=gpio_expansion_pin_height,
                      z_offset=-gpio_expansion_header_height,
                      p=0.65,
                      center=true);
        }
      }
      translate([-w / 2 + rpi_pin_header_width * 4,
                 -l / 2
                 + rpi_pin_header_width
                 * rpi_pin_headers_cols / 2
                 + rpi_bolts_offset * 2,
                 h]) {
        union() {
          pin_header(cols=rpi_pin_headers_cols,
                      rows=rpi_pin_headers_rows,
                      header_width=rpi_pin_header_width,
                      header_height=0,
                      pin_height=gpio_expansion_pin_height,
                      z_offset=0,
                      p=0.65,
                      center=true);
          let (total_x = rpi_pin_header_width * rpi_pin_headers_rows,
               total_y = rpi_pin_header_width * rpi_pin_headers_cols) {
            pin_header(cols=rpi_pin_headers_cols,
                        rows=rpi_pin_headers_rows,
                        header_width=rpi_pin_header_width,
                        header_height=0,
                        pin_height=gpio_expansion_pin_up_height,
                        z_offset=0,
                        p=0.65,
                        center=true);
            translate([0, 0, 0]) {
              color(yellow_1, alpha=1) {
                cube_3d([total_x, total_y, gpio_expansion_header_up_height]);
              }
            }
          }
        }
      }
      let (step = gpio_expansion_inner_header_gap +
           gpio_expansion_inner_header_rows * rpi_pin_header_width,
           total_y = step * (gpio_expansion_inner_headers_count - 1),) {
        translate([0, -total_y / 2, 0]) {
          for (i = [0 : gpio_expansion_inner_headers_count - 1]) {
            let (y = i * step,
                 total_x = rpi_pin_header_width * gpio_expansion_inner_header_rows,
                 total_y = rpi_pin_header_width * gpio_expansion_inner_header_cols) {
              translate([0, y, 0]) {
                rotate([0, 0, 90]) {
                  translate([0, 0, h]) {
                    pin_header(cols=gpio_expansion_inner_header_cols,
                                rows=gpio_expansion_inner_header_rows,
                                header_width=rpi_pin_header_width,
                                header_height=0,
                                pin_height=gpio_expansion_inner_header_pin_height,
                                z_offset=0,
                                p=0.65,
                                center=true);
                    color(yellow_1, alpha=1) {
                      cube_3d([total_x, total_y, gpio_expansion_header_up_height]);
                    }
                  }
                }
              }
            }
          }
        }
      }

      mirror_copy([0, 1, 0]) {
        translate([gpio_expansion_screw_terminal_x_offset,
                   -l / 2
                   + gpio_expansion_screw_terminal_thickness / 2,
                   h]) {
          rotate([0, 0, 180]) {
            screw_terminal(thickness=gpio_expansion_screw_terminal_thickness,
                           base_h=gpio_expansion_screw_terminal_base_h,
                           top_l=gpio_expansion_screw_terminal_top_l,
                           top_h=gpio_expansion_screw_terminal_top_h,
                           contacts_n=gpio_expansion_screw_terminal_contacts_n,
                           contact_w=gpio_expansion_screw_terminal_contact_w,
                           contact_h=gpio_expansion_screw_terminal_contact_h,
                           pitch=gpio_expansion_screw_terminal_pitch,
                           colr=metallic_silver_1);
          }
        }
      }
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

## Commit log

2025-06-12 feat(scad): add head mount and wheels plate designs
    [head_mount.scad, wheels_plate_down.scad]
2025-06-12 refactor: Extract common modules to util.scad for reuse
    [util.scad, wheels_plate_down.scad]
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2025-06-14 refactor: correct tilt angle calculation in head_mount.scad
    [head_mount.scad]
2025-06-14 refactor: simplify side panel functions and adjust tilt angle
    [head_mount.scad]
2025-06-14 style: Remove comment and fix spacing in SCAD files
    [head_mount.scad, wheels_plate_down.scad]
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2025-06-16 fix: adjust Raspberry Pi screw size
    [chassis.scad]
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2025-06-16 feat: Add extra cutouts and adjust dimensions in chassis design
    [chassis.scad, util.scad]
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2025-06-17 refactor: Adjust chassis dimensions and update screw placements
    [chassis.scad, main.scad, util.scad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]
2025-06-18 refactor: adjust dimensions and add new cutouts in SCAD files
    [back_mount.scad, chassis.scad, wheels_plate_down.scad]
2025-06-19 fix: correct dimensions for ups hat screws
    [chassis.scad]
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2025-06-21 refactor: clean up chassis module by removing unused variables
    [chassis.scad]
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2025-06-21 refactor: improve battery holder screw modules and parameters
    [chassis.scad, parameters.scad]
2025-06-21 refactor: Simplify servo hole distances with number_sequence function
    [head_mount.scad]
2025-06-21 style: Remove semicolons from use statements in SCAD files
    [chassis.scad, front_panel.scad, head_mount.scad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]
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2025-06-22 refactor: add back mount module to front panel
    [front_panel.scad, util.scad]
2025-06-22 refactor: move some head variables to the parameters
    [head_mount.scad, parameters.scad]
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2025-06-22 feat: Add ultrasonic screw holes to front panel design
    [front_panel.scad, parameters.scad]
2025-06-22 feat: add steering knuckle components to steering system
    [parameters.scad, steering_system.scad]
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2025-06-27 refactor: modularize steering system and add demo assembly
    [ackermann.scad, ackermann_assembly.scad, chassis.scad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]
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2025-07-02 refactor: modularize wheel components and update wheel usage
    [demo.scad, front_wheel.scad, parameters.scad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]
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2025-07-05 feat: add rack and pinion steering system components
    [bracket.scad, parameters.scad, pinion.scad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]
2025-07-05 refactor: adjust rack and knuckle dimensions for improved fit
    [parameters.scad, rack_and_pinion.scad, rack_knuckle.scad]
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2025-07-06 fix: increase distance between pinion and rack
    It prevents servo from buzzing
    [parameters.scad]
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2025-07-06 refactor: modularize rack and pinion assembly into separate file
    [rack_and_pinion.scad, rack_and_pinion_assembly.scad]
2025-07-06 refactor: modularize steering servo panel into separate file
    [parameters.scad, rack_and_pinion_assembly.scad, steering_servo_panel.scad]
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2025-07-08 fix: adjust bracket translation for correct alignment
    [bracket.scad]
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2025-07-12 refactor: remove old steering components and clean up code
    [ackermann.scad, ackermann_assembly.scad, bracket.scad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]
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2025-07-13 refactor: optimize servo slot placement logic in head_mount
    [head_mount.scad]
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2025-07-13 refactor: Add bearing shaft module and update knuckle connector usage
    [bearing_shaft.scad, knuckle.scad, steering_servo_panel.scad]
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2025-07-17 refactor: consolidate assembly and chassis modules in SCAD files
    [assembly.scad, ball_bearing.scad, chassis.scad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]
2025-07-19 refactor: reorganize and enhance SCAD files for steering system
    [assembly.scad, ball_bearing.scad, bearing_connector.scad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]
2025-07-19 fix: adjust knuckle bearing inner diameter for better fit
    [parameters.scad]
2025-07-20 refactor: update steering system with new knuckle shaft and bearing modules
    [assembly.scad, bearing.scad, bracket.scad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]
2025-07-20 refactor: update knuckle shaft and connector design for improved fit
    [knuckle.scad, knuckle_shaft.scad, parameters.scad]
2025-07-20 refactor: update screw hole size parameter for Raspberry Pi 5
    [chassis.scad, parameters.scad]
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2025-07-20 refactor: rename and simplify knuckle shaft print plate module
    [knuckle_shaft.scad]
2025-07-20 refactor: improve readability of steering servo panel code
    [steering_servo_panel.scad]
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2025-07-22 refactor: Adjust wheel and tire parameters for improved fit
    [parameters.scad, tire.scad, wheel.scad]
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2025-07-24 refactor: enhance motor and chassis modularity in SCAD files
    [assembly.scad, chassis.scad, head_assembly.scad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]
2025-07-25 feat: redesign steering panel
    [parameters.scad, rack_and_pinion_assembly.scad, rear_panel.scad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]
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2025-07-26 style: Add braces for nested offset in trapezoid_rounded module
    [util.scad]
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2025-07-27 fix: correct position of front panel's connector
    [front_panel.scad]
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2025-07-27 fix: add missing module
    [ackermann_geometry_triangle.scad]
2025-07-27 fix: correct the knuckle connector with holes not rendered correctly
    [knuckle.scad, knuckle_connector.scad]
2025-07-27 docs: Add module headers to some steering system files
    [ackermann_geometry_triangle.scad, rack.scad]
2025-07-29 refactor: show back mount in the front panel
    [front_panel.scad]
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2025-07-29 fix: correct wheel rendering with convexity
    [wheel.scad]
2025-07-29 fix: correct shaft hole depth in rear wheel
    [rear_wheel.scad]
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2025-07-30 fix: correct bearing placement in knuckle
    [knuckle.scad]
2025-07-30 refactor: reverse bearing placement in bracket
    [bracket.scad]
2025-07-30 feat: add vertical and direction options to row_of_circles module
    [util.scad]
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2025-07-30 feat: add pinion display option to steering servo panel
    [servo.scad, steering_servo_panel.scad]
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2025-07-30 feat: use new gear in rack and pinion
    [parameters.scad, pinion.scad, rack.scad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]
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2025-08-02 feat: Redesign chassis, wheels, add Raspberry Pi 5 and UPS HAT
    [assembly.scad, battery.scad, chassis.scad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]
2025-08-03 refactor: make the bracket for n20-motor a bit wider
    [n20_motor_bracket.scad, standard_motor_bracket.scad]
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2025-08-03 fix: correct loop condition in steering servo module
    [chassis.scad]
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2025-08-03 refactor: improve n20 motor bracket design and add tolerance parameter
    [n20_motor_bracket.scad, parameters.scad]
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2025-08-04 style: Fix spacing in head module
    [head_mount.scad]
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2025-08-16 refactor: update steering system reversal logic and parameter names
    [knuckle.scad, knuckle_shaft.scad, parameters.scad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]
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2025-08-16 docs: fix URL in IR LED placeholder model comments
    [ir_led.scad]
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2025-08-17 fix: update n20 motor bracket assembly to hide motor by default
    [n20_motor_bracket.scad]
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2025-08-17 fix: adjust N20 motor bracket tolerance to 0.2
    [parameters.scad]
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2025-08-18 style: fix indentation in front_panel
    [front_panel.scad]
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2025-08-30 refactor: improve head and camera modules
    - Place the top camera in the head slightly higher so it is easier to insert the FFC cable.
    - Add an FFC connector to the camera module placeholder.
    [camera.scad, head_mount.scad, parameters.scad]
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2025-08-30 refactor: redesign steering system
    [assembly.scad, bracket.scad, knuckle.scad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]
2025-08-31 fix: remove alpha parameter from steering_pinion call
    [steering_servo_mount.scad]
2025-09-02 feat: implement true Ackermann steering geometry
    Redesign the steering system to make Ackermann geometry work correctly.
    Also make most steering-system components attachable.
    [ackermann_geometry_triangle.scad, assembly.scad, bearing_connector.scad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]
2025-09-02 docs: correct default Raspberry Camera Module version
    [head_neck.scad]
2025-09-02 style: Correct spelling of 'metallic' in color definitions
    [battery_holder.scad, bearing.scad, colors.scad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]
2025-09-02 fix: correct steering chassis bar
    [steering_panel.scad]
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2025-12-07 refactor: use fixed value for chassis trapezoid shape
    [parameters.scad]
2025-12-08 feat: Add AI HAT, GPIO expansion, servo driver and motor driver HATs
    [ai_hat.scad, assembly.scad, bcm.scad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]
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2025-12-11 fix: correct tie rod geometry for variable wheelbase
    [parameters.scad]
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2025-12-22 refactor: redesign and split chassis into components
    [ackermann_geometry_triangle.scad, assembly.scad, bolt.scad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]
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2025-12-23 fix: use standoff stack instead of invalid thread d
    [ai_hat.scad, gpio_expansion_board.scad, motor_driver_hat.scad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]
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2025-12-24 fix: apply pan_servo_rotation via servo horn and head transform
    [head_neck.scad]
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2025-12-25 fix(scad): correct rect_slot recess extrusion and reverse example
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2025-12-26 fix: add round_side option and convexity to xt90 placeholders
    [xt90.scad, xt90e-m.scad]
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2025-12-29 fix: correct fuse holder wiring points and socket case wiring paths
    [atm_fuse_holder.scad, parameters.scad, power_socket_case.scad]
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2025-12-31 fix: default screw terminal base_w from plist-derived width
    [screw_terminal.scad]
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2026-01-03 fix: add upper header and pin height params for motor driver hat
    [parameters.scad]
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2026-01-03 fix: add convexity to knuckle connector extrusions
    [knuckle_connector.scad]
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2026-01-04 refactor: modularize ATM fuse holder and add slot/reverse options
    [atm_fuse_holder.scad, parameters.scad]
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2026-01-04 fix: refine kingpin post bolt holes seam and cylinder resolution
    [steering_kingpin_post.scad]
2026-01-04 fix: add missing modules
    [atm_fuse_holder_body.scad, atm_fuse_holder_cap.scad, atm_fuse_holder_cap_collar.scad]
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2026-01-05 refactor: replace smd battery holder with slot grid system
    [assembly.scad, atm_fuse_holder.scad, atm_fuse_holder_body.scad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]
2026-01-05 fix: default perf_board placeholder to centered placement
    [perf_board.scad]
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2026-01-05 fix: center toggle switch counterbore and panel bolt counterbores
    [control_panel.scad, toggle_switch.scad]
2026-01-05 fix: center fuse panel bolt counterbore and remove debug cube
    [fuse_panel.scad]
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2026-01-06 fix: correct UPS hat placement and make it optional
    [assembly.scad, chassis_body.scad, parameters.scad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]
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2026-01-07 fix: correct position of power socket case on chassis
    [chassis_body.scad]
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2026-01-07 fix: remove outdated show_smd_battery_holders parameter
    [chassis_printable.scad]
2026-01-07 fix: reduce battery holder tab slot extra width to 4
    [parameters.scad]
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2026-01-09 fix: correct upper chassis trapezoids borders
    [parameters.scad, upper_chassis.scad]
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2026-01-10 fix: correct socket's Z position
    [power_socket_case.scad]
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2026-01-14 fix: escape Makefile vars and pass colors to steering panel printable
    [steering_panel.scad, steering_panel_printable.scad]
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2026-01-16 fix(scad): wrap shaft ring color block and call bearing with rings
    [bearing.scad]
